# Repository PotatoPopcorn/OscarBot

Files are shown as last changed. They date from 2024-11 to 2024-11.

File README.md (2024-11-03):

# OscarBot

This is the repository of the code and 3D print files for my thesis. Below is a list of additional parts used

<table>
  <tr>
    <th>Part Name</th>
    <th>Quantity</th>
    <th>Link to Part</th>
    <th>Notes</th>
  </tr>
  <tr>
    <td>Raspberry Pi 4B 8GB</td>
    <td>1</td>
    <td><a href="https://core-electronics.com.au/raspberry-pi-4-model-b-8gb.html">https://core-electronics.com.au/raspberry-pi-4-model-b-8gb.html</a></td>
    <td></td>
  </tr>
  <tr>
    <td>USB Battery Bank</td>
    <td>1</td>
    <td><a href="https://www.jbhifi.com.au/products/cygnett-chargeup-boost-gen3-5k-power-bank-black?ab_version=B">https://www.jbhifi.com.au/products/cygnett-chargeup-boost-gen3-5k-power-bank-black?ab_version=B</a></td>
    <td>Not identical to the one used, but I cannot find details for it</td>
  </tr>
  <tr>
    <td>Jaycar 4WD Kit</td>
    <td>1</td>
    <td><a href="https://www.jaycar.com.au/4-wheel-drive-motor-chassis-robotics-kit/p/KR3162">https://www.jaycar.com.au/4-wheel-drive-motor-chassis-robotics-kit/p/KR3162</a></td>
    <td>Used for various parts in the project</td>
  </tr>
  <tr>
    <td>Omni Wheels</td>
    <td>4</td>
    <td><a href="https://www.rotacaster.com.au/shop/35mm-omni-wheels/index">https://www.rotacaster.com.au/shop/35mm-omni-wheels/index</a></td>
    <td></td>
  </tr>
  <tr>
    <td>Motor Controller</td>
    <td>2</td>
    <td><a href="https://www.jaycar.com.au/arduino-compatible-stepper-motor-controller-module/p/XC4492">https://www.jaycar.com.au/arduino-compatible-stepper-motor-controller-module/p/XC4492</a></td>
    <td></td>
  </tr>
  <tr>
    <td>Arduino Unos</td>
    <td>2</td>
    <td><a href="https://www.jaycar.com.au/duinotech-uno-r3-main-board/p/XC4410">https://www.jaycar.com.au/duinotech-uno-r3-main-board/p/XC4410</a></td>
    <td></td>
  </tr>
  <tr>
    <td>AA Battery Holder</td>
    <td>2</td>
    <td><a href="https://www.jaycar.com.au/6-x-aa-2-by-3-side-by-side-battery-holder/p/PH9206">https://www.jaycar.com.au/6-x-aa-2-by-3-side-by-side-battery-holder/p/PH9206</a></td>
    <td>Wired in parallel</td>
  </tr>
  <tr>
    <td>Servo Controller</td>
    <td>1</td>
    <td><a href="https://tribotix.com/product/openrb-150/">https://tribotix.com/product/openrb-150/</a></td>
    <td></td>
  </tr>
  <tr>
    <td>Servo Motors</td>
    <td>6</td>
    <td><a href="https://tribotix.com/product/xl330-m288-t/">https://tribotix.com/product/xl330-m288-t/</a></td>
    <td></td>
  </tr>
</table>

As well as various USB cables, jumper cables and hookup wire.

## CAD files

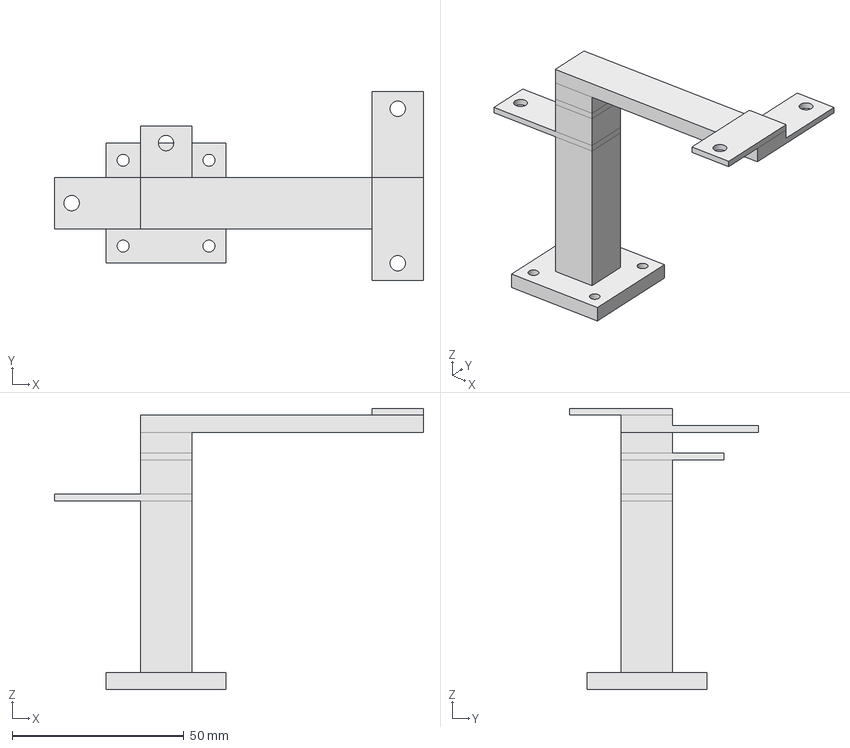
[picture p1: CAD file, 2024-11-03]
Freecad/TrackerHolderV1.FCStd
107.5 x 55.0 x 82.0 mm

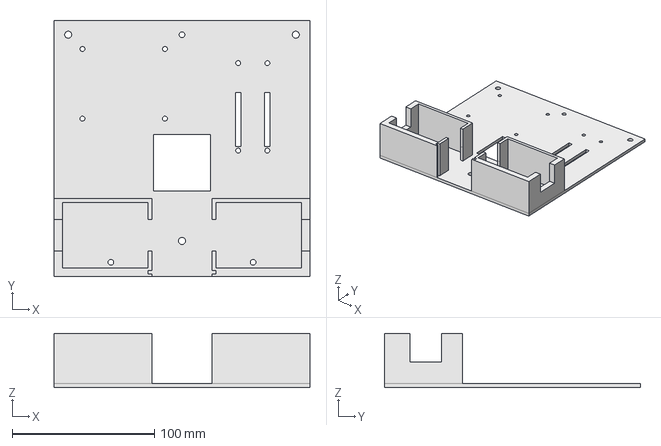
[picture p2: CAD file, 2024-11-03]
Freecad/ThesisMiddlePlate V3.FCStd
180.0 x 180.0 x 38.0 mm

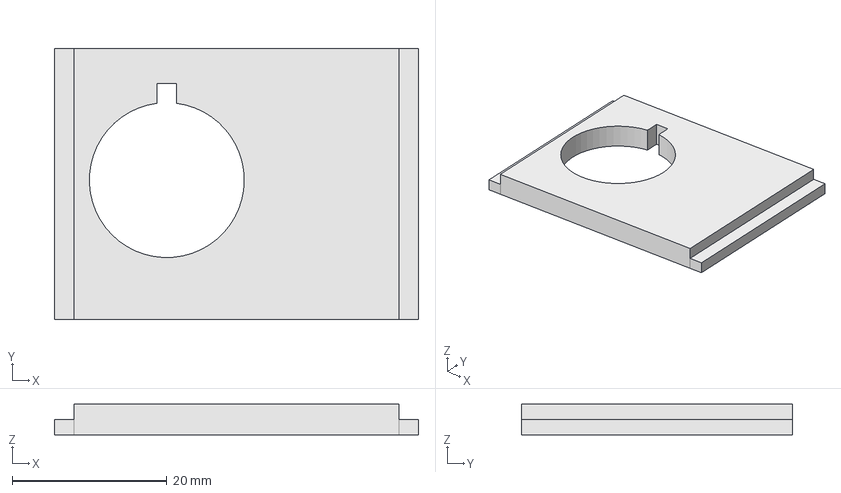
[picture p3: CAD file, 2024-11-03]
Freecad/SwitchHolder.FCStd
47.0 x 35.0 x 4.00 mm

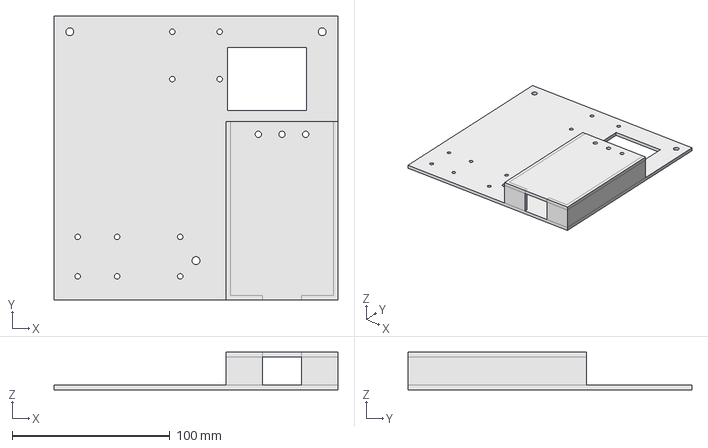
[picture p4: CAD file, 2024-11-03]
Freecad/ThesisTopPlateV4.FCStd
180.0 x 180.0 x 24.0 mm

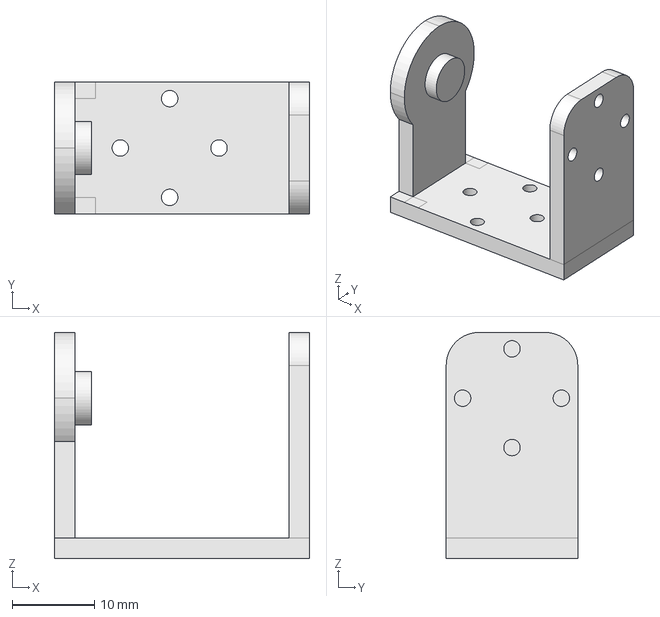
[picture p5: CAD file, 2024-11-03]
Freecad/TiltAdapterGripperV1.FCStd
31.0 x 16.0 x 27.5 mm

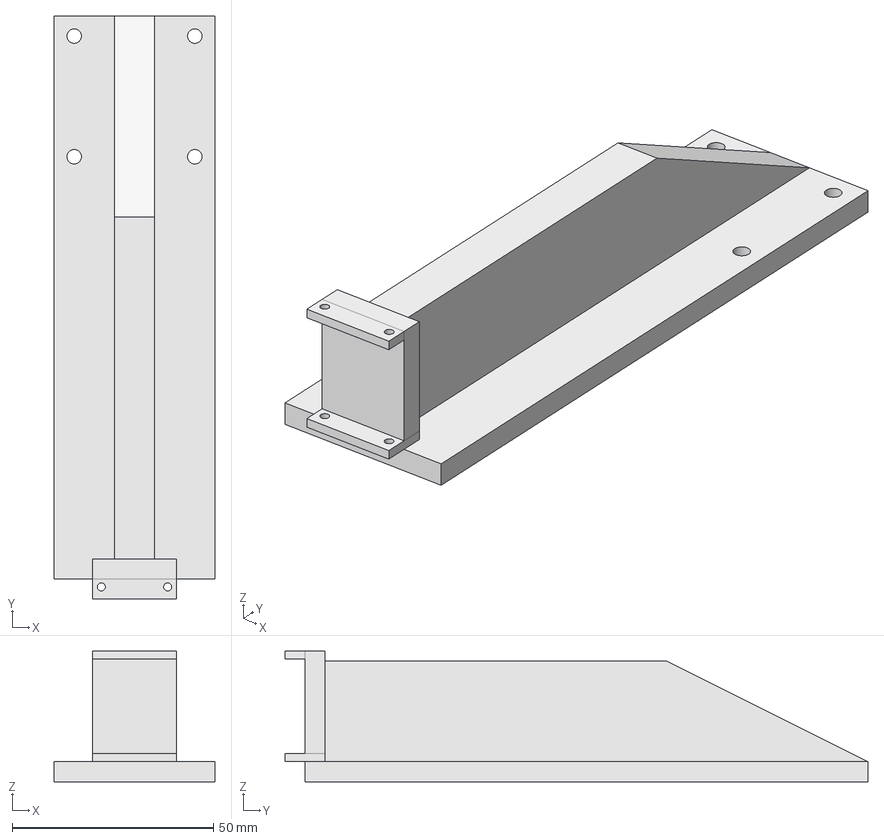
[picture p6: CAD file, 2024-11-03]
Freecad/GripperAttachV4.FCStd
40.0 x 145.0 x 32.5 mm

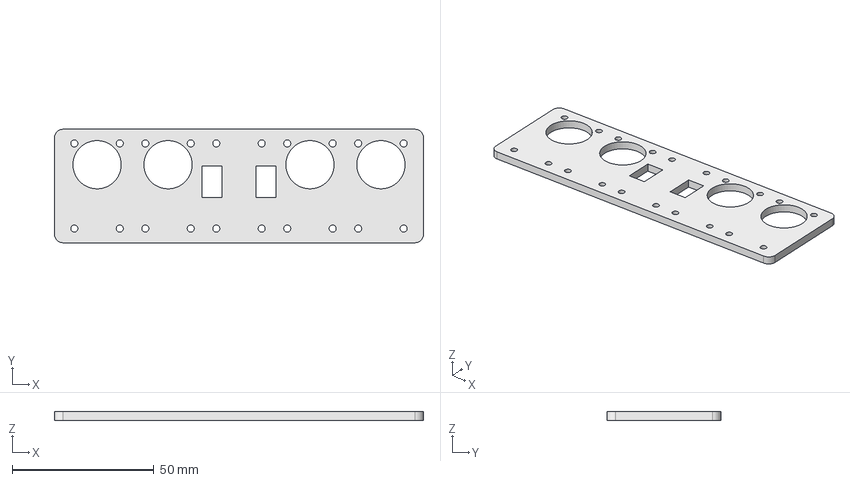
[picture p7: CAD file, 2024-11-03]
Freecad/BasePlate.FCStd
130.0 x 40.0 x 3.00 mm

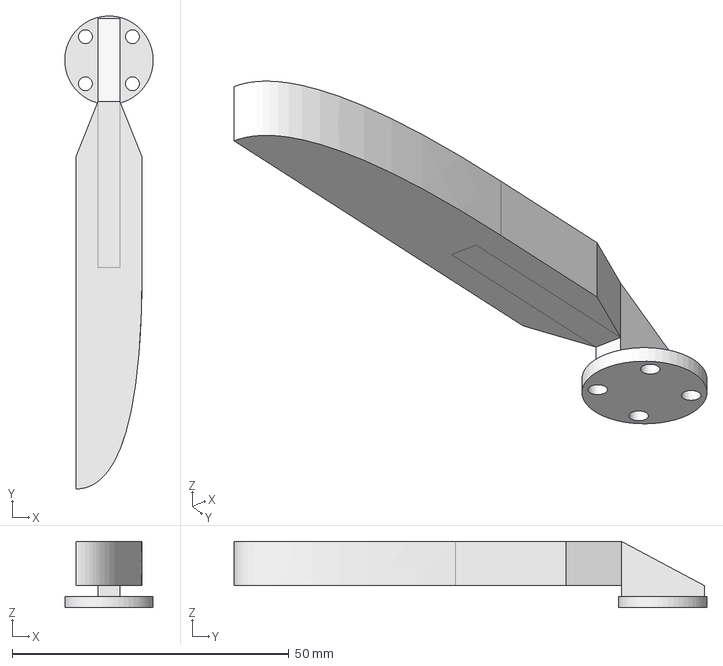
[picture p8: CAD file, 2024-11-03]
Freecad/Finger.FCStd
16.0 x 85.5 x 12.0 mm

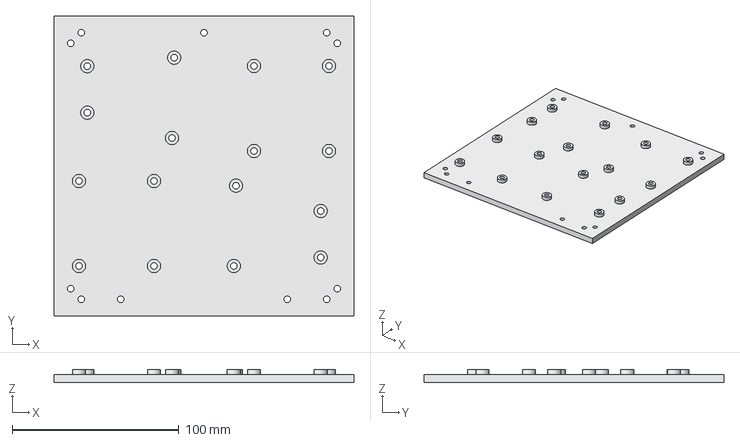
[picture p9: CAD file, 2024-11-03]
Freecad/ThesisBasePlate V2.FCStd
180.0 x 180.0 x 8.00 mm

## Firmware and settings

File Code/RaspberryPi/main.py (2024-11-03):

import math
import time
import traceback

from datetime import datetime

import numpy as np

import gripper_handler
import motor_handler
import oscar_kinematics
import pid_controller
import serial_handler
import tracker_handler
import tracker_kinematics
import unity_handler

try:
    serial_handle = serial_handler.SerialHandler()
except serial_handler.SerialSetupException as exc:
    print(exc)
    exit()

input("Press Enter to start movements\n")

dynamixel = serial_handle.get_dynamixel_path()

gripper = gripper_handler.GripperHandler(dynamixel)

gripper.enable_gripper()

motors = motor_handler.MotorHandler(serial_handle)

unity = unity_handler.UnityHandler(gripper, motors)

track = tracker_handler.TrackerHandler()

kine = tracker_kinematics.TrackerKinematics()

pid_x = pid_controller.PIDControl(0.0025, 0.0007, 0)#, static_factor = 500000, static_ki = 50000, static_limit=200)
pid_y = pid_controller.PIDControl(0.0025, 0.0007, 0)#, static_factor = 500000, static_ki = 50000, static_limit=200)
pid_rot = pid_controller.PIDControl(0.1, 0.05, 0, static_factor = 0.1)# (0.5, 0.2, 0) #, static_factor = 0.5)

stop_counter = 0

def auto_mode():
    
    rot = oscar_kinematics.get_difference_in_euler_angles(
       track.get_robot_track()['rotation_euler']['Z'],
       0
       )



    kine.setRootPositionAndRotation([track.get_robot_track()['location']['X'], track.get_robot_track()['location']['Y'], track.get_robot_track()['location']['Z']], track.get_robot_track()['rotation_matrix'])
    offset = kine.getLocalPosition([0, 0, 0])
    
    off_x = pid_x.update(offset[0], 0)
    off_y = pid_y.update(offset[1], 0)

    print("RECORD:", rot, offset, np.sqrt(offset[0]*offset[0]+offset[1]*offset[1]), datetime.now())

    off_rot = pid_rot.update(rot, 0)
    # print(rot, cont)
    motors.move(off_x, off_y, off_rot)

#    if np.abs(pid_x.speed) > 0.0001 or np.abs(pid_y.speed) > 0.0001:
#        print("DIST:", np.sqrt((offset[0]) ** 2 + (offset[1]) ** 2), "SPEED X:", pid_x.speed, "Y:", pid_y.speed)
#        gripper.set_gripper_pan(np.pi)
#        if np.sqrt((offset[0]) ** 2 + (offset[1]) ** 2) < 15 and np.abs(rot) < 0.15:
#            gripper.set_gripper_tilt(7 * np.pi / 6)
#            stop_counter += 1
#            if stop_counter > 25:
#                gripper.close_left()
#            if stop_counter > 50:
#                break

#        else:
#            gripper.set_gripper_tilt(np.pi)
#            stop_counter = 0
#            gripper.open_left()

try:
    while True:
        if "mode" in unity.last_data:
            if unity.last_data["mode"] == 1:
                pid_x.reset()
                pid_y.reset()
                pid_rot.reset()
                unity.drive_manual(unity.last_data)
            elif unity.last_data["mode"] == 2:
                auto_mode()
                # print("Auto Mode")
        else:
            # print("Inactive")
            motors.move(0, 0, 0)
        #print(f"31: {gripper._get_link_current(31)}, 34: {gripper._get_link_current(34)}")
except Exception as exc:
    traceback.print_exc()
    motors.move(0, 0, 0)


motors.move(0, 0, 0)

gripper.set_gripper_tilt(np.pi / 2)

time.sleep(5)

gripper.disable_gripper()

# left_arduino.write(bytes("IDU05FFFF1000\r\n", "ASCII"))
# right_arduino.write(bytes("IDU06FFFF1000\r\n", "ASCII"))

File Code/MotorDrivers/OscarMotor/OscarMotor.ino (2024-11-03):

#define VER_MAJ 2
#define VER_MIN 0
#define VER_HOT 1

#define ENA 11
#define ENB 10
#define IN1 13
#define IN2 12
#define IN3 8
#define IN4 9

#define SIDE_LEFT 'L'
#define SIDE_RIGHT 'R'
#define SIDE_UNKNOWN 'U'

#define CMD_LEN 32

#define LEFT_MIN 1020
#define RIGHT_MIN 650
#define RIGHT_MAX 700
char cmd[CMD_LEN];

int counter = 0;
unsigned char convres;

void clear_cmd() {
  memset(cmd, 0, CMD_LEN);
}

bool cmp_cmd(char* needle) {
  return memcmp(cmd, needle, 3) == 0;
}

void set_pins(char pin, char offset, char input) {
  char res = bitRead(input, offset);
  if(res == 1) {
    digitalWrite(pin, HIGH);
  } else {
    digitalWrite(pin, LOW);
  }
}

bool convert_digit(char digit, unsigned char* out) {
    if (digit >= 0x30 && digit <= 0x39) {
        *out += digit - 0x30;
        return true;
    } else if (digit >= 'A' && digit <= 'F') {
        *out += digit - 'A' + 10;
        return true;
    } else if (digit >= 'a' && digit <= 'f') {
        *out += digit - 'a' + 10;
        return true;
    }
    return false;
}

bool convert_byte(char digits[], unsigned char* out) {
    *out = 0;
    if(!convert_digit(digits[0], out)) {
        return false;
    }
    *out *= 16;
    if (!convert_digit(digits[1], out)) {
        return false;
    }
    return true;
}

char get_side() {
  char result = SIDE_UNKNOWN;
  int sample = 0;
  for (int i = 0; i < 4; ++i) {
    sample = analogRead(A0);
    if (result == SIDE_UNKNOWN && sample >= LEFT_MIN) {
      result = SIDE_LEFT;
    } else if (result == SIDE_LEFT && sample >= LEFT_MIN) {
      // Do Nothing, we have the correct side and the sample matches
    } else if (result == SIDE_LEFT && sample < LEFT_MIN) {
      return SIDE_UNKNOWN;
    } else if (result == SIDE_UNKNOWN && sample >= RIGHT_MIN && sample <= RIGHT_MAX) {
      result = SIDE_RIGHT;
    } else if (result == SIDE_RIGHT && sample >= RIGHT_MIN && sample <= RIGHT_MAX) {
      // Do Nothing, we have the correct side and the sample matches
    } else if (result == SIDE_RIGHT && (sample < RIGHT_MIN || sample > RIGHT_MAX)) {
      return SIDE_UNKNOWN;
    } else {
      return SIDE_UNKNOWN;
    }
  }
  return result;
}

void handle_init() {
  Serial.write("INI");
  Serial.write(VER_MAJ);
  Serial.write(VER_MIN);
  Serial.write(VER_HOT);
  Serial.write(get_side());
  Serial.write("\n");
}

void handle_halt() {
  digitalWrite(IN1, LOW);
  digitalWrite(IN2, LOW);
  digitalWrite(IN3, LOW);
  digitalWrite(IN4, LOW);
  analogWrite(ENA, 0);
  analogWrite(ENB, 0);
}

void set_upper_pins(char* cmd) {
  convert_byte(cmd + 3, &convres);
  set_pins(IN1, 0, convres);
  set_pins(IN2, 1, convres);
  set_pins(IN3, 2, convres);
  set_pins(IN4, 3, convres);
  convert_byte(cmd + 5, &convres);
  analogWrite(ENA, convres);
  convert_byte(cmd + 7, &convres);
  analogWrite(ENB, convres);
}

void setup() {
  Serial.begin(115200);
  pinMode(ENA, OUTPUT);
  pinMode(ENB, OUTPUT);
  pinMode(IN1, OUTPUT);
  pinMode(IN2, OUTPUT);
  pinMode(IN3, OUTPUT);
  pinMode(IN4, OUTPUT);
  Serial.println("Started");
}

void loop() {
  //Serial.println(analogRead(A0));
  clear_cmd();
  if(Serial.available() > 0) {
    Serial.readBytesUntil('\n', cmd, CMD_LEN);
  }
  if(cmp_cmd("INI")) {
    handle_init();
  } else if (cmp_cmd("HAL")) {
    handle_halt();
  } else if (cmp_cmd("CDU")) {
    set_upper_pins(cmd);
  } else if (cmp_cmd("IDU")) {
    unsigned short wait_time = 0;
    set_upper_pins(cmd);
    convert_byte(cmd + 9, &convres);
    wait_time = convres * 256;
    convert_byte(cmd + 11, &convres);
    wait_time += convres;
    Serial.println(wait_time);
    delay(wait_time);
    handle_halt();
  }
}

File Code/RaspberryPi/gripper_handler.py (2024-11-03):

import math
import time

import dynamixel_sdk

class OscarBotArmException(Exception):
    pass

class GripperHandler:
    def __init__(self, device_name:str):
        self.active_dev_ids = [31, 32, 33, 34, 40, 42]
        self.PROTOCOL_VERSION = 2.0
        self.BAUDRATE = 57600
        self.DEVICENAME = device_name

        self.ADDR_TORQUE_ENABLE = 64
        self.ADDR_GOAL_POSITION = 116
        self.ADDR_PRESENT_CURRENT = 126
        self.ADDR_PRESENT_POSITION = 132
        self.ADDR_LED_ENABLE = 65
        self.DXL_MINIMUM_POSITION_VALUE = 0
        self.DXL_MAXIMUM_POSITION_VALUE = 4095

        self.TORQUE_ENABLE = 1
        self.TORQUE_DISABLE = 0
        self.DXL_MOVING_STATUS_THRESHOLD = 20

        self.target_close_offset = 0.05

        #self.is_left_closed = False
        #self.is_right_closed = False

        self.portHandler = dynamixel_sdk.PortHandler(self.DEVICENAME)
        self.packetHandler = dynamixel_sdk.PacketHandler(self.PROTOCOL_VERSION)
        if not self.portHandler.openPort():
            raise OscarBotArmException("Could not open port")

        if not self.portHandler.setBaudRate(self.BAUDRATE):
            raise OscarBotArmException("Could not change baudrate")

    def _test_ping(self, dev_id:int):
        dxl_model_number, dxl_comm_result, dxl_error = self.packetHandler.ping(self.portHandler, dev_id)
        if dxl_comm_result != dynamixel_sdk.COMM_SUCCESS:
            raise OscarBotArmException(f"Failed to ping device with ID: {dev_id} - "
                                    f"{self.packetHandler.getTxRxResult(dxl_comm_result)}")
        elif dxl_error != 0:
            raise OscarBotArmException(f"Failed to ping device with ID: {dev_id} - "
                                    f"{self.packetHandler.getRxPacketError(dxl_error)}")

    def _set_led(self, dev_id:int, state:bool):
        led_mode = self.TORQUE_ENABLE if state else self.TORQUE_DISABLE
        dxl_comm_result, dxl_error = self.packetHandler.write1ByteTxRx(self.portHandler, dev_id, self.ADDR_LED_ENABLE, led_mode)
        if dxl_comm_result != dynamixel_sdk.COMM_SUCCESS:
            raise OscarBotArmException(f"Failed to set torque of device with ID: {dev_id} - "
                                    f"{self.packetHandler.getTxRxResult(dxl_comm_result)}")
        elif dxl_error != 0:
            raise OscarBotArmException(f"Failed to set torque of device with ID: {dev_id} - "
                                    f"{self.packetHandler.getRxPacketError(dxl_error)}")

    def _set_enable_torque(self, dev_id:int, state:bool):
        torque_mode = self.TORQUE_ENABLE if state else self.TORQUE_DISABLE
        dxl_comm_result, dxl_error = self.packetHandler.write1ByteTxRx(self.portHandler, dev_id, self.ADDR_TORQUE_ENABLE, torque_mode)
        if dxl_comm_result != dynamixel_sdk.COMM_SUCCESS:
            raise OscarBotArmException(f"Failed to set torque of device with ID: {dev} - "
                                   f"{self.packetHandler.getTxRxResult(dxl_comm_result)}")
        elif dxl_error != 0:
            raise OscarBotArmException(f"Failed to set torque of device with ID: {dev} - "
                                   f"{self.packetHandler.getRxPacketError(dxl_error)}")

    def _set_link_angle(self, link_id: int, angle: float):
        angle = int(angle * self.DXL_MAXIMUM_POSITION_VALUE / (2 * math.pi))
        dxl_comm_result, dxl_error = self.packetHandler.write4ByteTxRx(self.portHandler, link_id, self.ADDR_GOAL_POSITION, angle)
        if dxl_comm_result != dynamixel_sdk.COMM_SUCCESS:
            raise OscarBotArmException(f"Failed to set angle of device with ID: {link_id} - "
                                       f"{self.packetHandler.getTxRxResult(dxl_comm_result)}")
        elif dxl_error != 0:
            raise OscarBotArmException(f"Failed to set angle of device with ID: {link_id} - "
                                       f"{self.packetHandler.getRxPacketError(dxl_error)}")

    def _get_link_angle(self, link_id: int):
        dxl_present_position, dxl_comm_result, dxl_error = self.packetHandler.read4ByteTxRx(self.portHandler, link_id, self.ADDR_PRESENT_POSITION)
        if dxl_comm_result != dynamixel_sdk.COMM_SUCCESS:
            raise OscarBotArmException(
                f"Failed to get angle of device with ID: {link_id} - {self.packetHandler.getTxRxResult(dxl_comm_result)}")
        elif dxl_error != 0:
            raise OscarBotArmException(
                f"Failed to get angle of device with ID: {link_id} - {self.packetHandler.getRxPacketError(dxl_error)}")
        angle = dxl_present_position * (2 * math.pi) / self.DXL_MAXIMUM_POSITION_VALUE
        return angle

    def _get_link_current(self, link_id: int):
        dxl_present_current, dxl_comm_result, dxl_error = self.packetHandler.read2ByteTxRx(self.portHandler, link_id, self.ADDR_PRESENT_CURRENT)
        if dxl_comm_result != dynamixel_sdk.COMM_SUCCESS:
            raise OscarBotArmException(
                f"Failed to get current of device with ID: {link_id} - {self.packetHandler.getTxRxResult(dxl_comm_result)}")
        elif dxl_error != 0:
            raise OscarBotArmException(
                f"Failed to get current of device with ID: {link_id} - {self.packetHandler.getRxPacketError(dxl_error)}")
        print(dxl_present_current)
        out_current = dxl_present_current if dxl_present_current < 2 ** 15 else dxl_present_current - 2 ** 16 
        return out_current

    def enable_gripper(self):
        for dev_id in self.active_dev_ids:
            self._set_led(dev_id, True)
            self._set_enable_torque(dev_id, True)
        self._set_link_angle(32, 1.25 * math.pi)
        self._set_link_angle(33, 0.75 * math.pi)
    
    def disable_gripper(self):
        for dev_id in self.active_dev_ids:
            self._set_enable_torque(dev_id, False)
            self._set_led(dev_id, False)

    def open_left(self):
        self._set_link_angle(31, math.pi)
    
    def close_left(self):
        # TODO: if this isn't sufficient, figure out how to read current values
        self._set_link_angle(31, (0.75 + self.target_close_offset) * math.pi)

    def open_right(self):
        self._set_link_angle(34, math.pi)
        #self.is_right_closed = False
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

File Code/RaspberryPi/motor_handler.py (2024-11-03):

import numpy as np

import oscar_kinematics 
import serial_handler

WHEEL_CONFIG = {
    'nw': {
        'serial': 2,
        'shift': 2,
        'dir': False
    },
    'ne': {
        'serial': 1,
        'shift': 0,
        'dir': True
    },
    'se': {
        'serial': 1,
        'shift': 2,
        'dir': False
    },
    'sw': {
        'serial': 2,
        'shift': 0,
        'dir': False
    }
}

class MotorHandler:
    def __init__(self, serial: serial_handler.SerialHandler):
        self.left = serial.get_left_serial() 
        self.right = serial.get_right_serial()

    def _decode_wheel_information(self, dir, settings):
        r2 = np.min([255, np.floor(dir*255)])
        if dir < 0.001 and dir > -0.001:
            return 0, 0
        elif dir < 0:
            r1 = 1 if settings["dir"] else 2
            r2 *= -1
        else:
            r1 = 2 if settings["dir"] else 1

        r1 = r1 << settings["shift"]

        return r1, int(r2)

    def move(self, x1:float, x2:float, rot:float):
        nw, ne, se, sw = oscar_kinematics.wheel_movment_kinematics(x1, x2, rot)
        nw1, nw2 = self._decode_wheel_information(nw, WHEEL_CONFIG['nw'])
        ne1, ne2 = self._decode_wheel_information(ne, WHEEL_CONFIG['ne'])
        se1, se2 = self._decode_wheel_information(se, WHEEL_CONFIG['se'])
        sw1, sw2 = self._decode_wheel_information(sw, WHEEL_CONFIG['sw'])

        wdir = nw1 + sw1
        edir = ne1 + se1

        frame1 = bytearray(b'CDU')
        frame2 = bytearray(b'CDU')

        frame1.extend(bytes(f"{edir:02x}", "ascii"))
        frame2.extend(bytes(f"{wdir:02x}", "ascii"))

        frame1.extend(bytes(f"{ne2:02x}", "ascii"))
        frame1.extend(bytes(f"{se2:02x}\n", "ascii"))
        frame2.extend(bytes(f"{sw2:02x}", "ascii"))
        frame2.extend(bytes(f"{nw2:02x}\n", "ascii"))

        self.right.write(bytes(frame1))
        self.left.write(bytes(frame2))        

    def stop(self):
        self.left.write(b"HAL\n")
        self.right.write(b"HAL\n")
